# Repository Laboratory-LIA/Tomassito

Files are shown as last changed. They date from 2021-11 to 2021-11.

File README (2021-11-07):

README Tomassito V 0.9

The RobotCar Tomassito project is a development of "Applied Innovation Laboratory" of the informatics area
of the Santo Tomás Professional Institute, San Joaquín Campus.

Project distributed under Creative Commons Attribution License CC BY

Feel free to generate derivative developments, share and build robot, let's democratize technology.

Make us happy, follow our project

https://github.com/Laboratory-LIA/Tomassito/

/-/-/-/-/-/-/-/-/-/-/-/-/-/-/-/-/-/-/-/

README Tomassito V 0.9

El proyecto de RobotCar Tomassito es un desarrollo de "Laboratorio de Innovación Aplicada" del área de informática
del Instituto profesional Santo Tomás sede San Joaquín.

Proyecto distribuido bajo Licencia Creative Commons de Atribución CC BY

Siéntase libre de generar desarrollos derivados, compartir y construir robot, democraticemos la tecnología.

haznos felices, sigue nuestro proyecto

https://github.com/Laboratory-LIA/Tomassito/

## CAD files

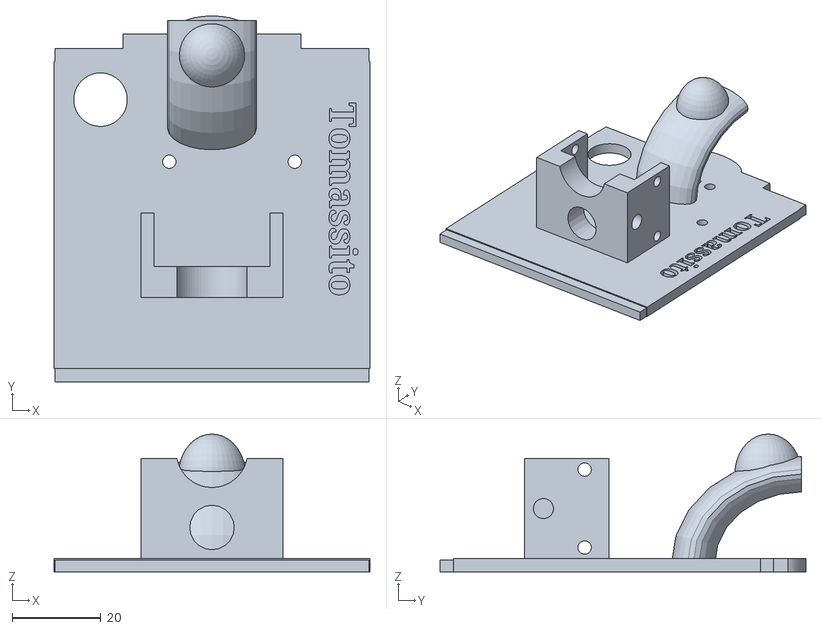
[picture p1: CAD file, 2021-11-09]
STL V0.9/Base.stl
71.0 x 82.3 x 31.0

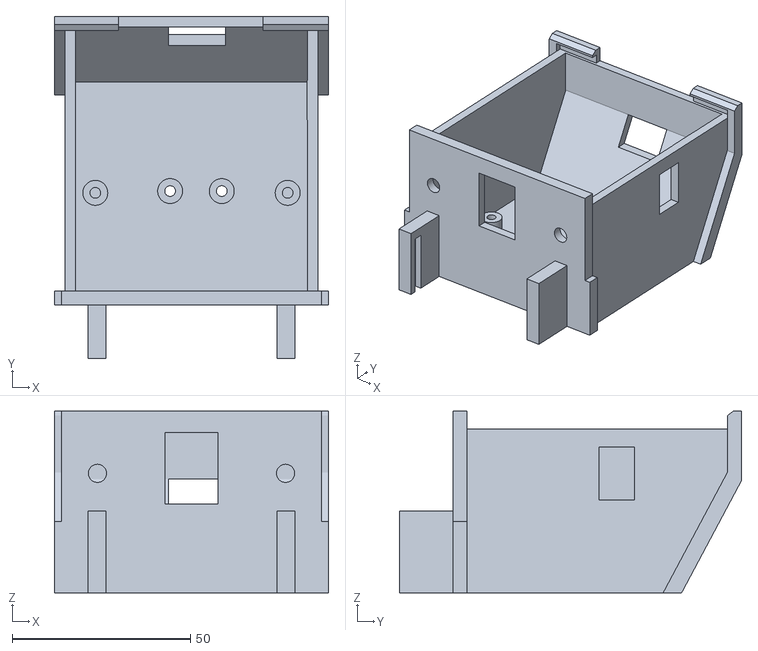
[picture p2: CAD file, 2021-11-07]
STL V0.9/Cuerpo.stl
77.0 x 96.0 x 51.0

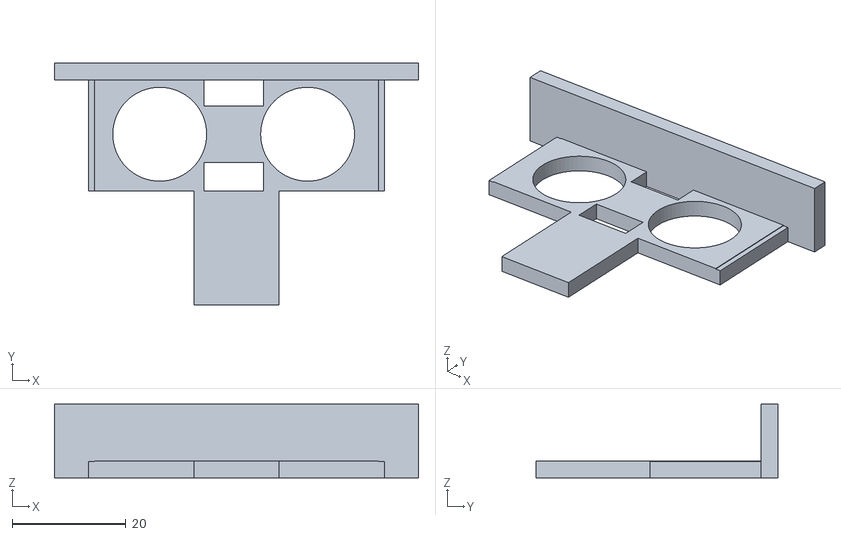
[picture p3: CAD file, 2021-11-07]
STL V0.9/Ojos.stl
64.0 x 42.5 x 13.0

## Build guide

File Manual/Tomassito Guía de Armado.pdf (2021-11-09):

| 2021

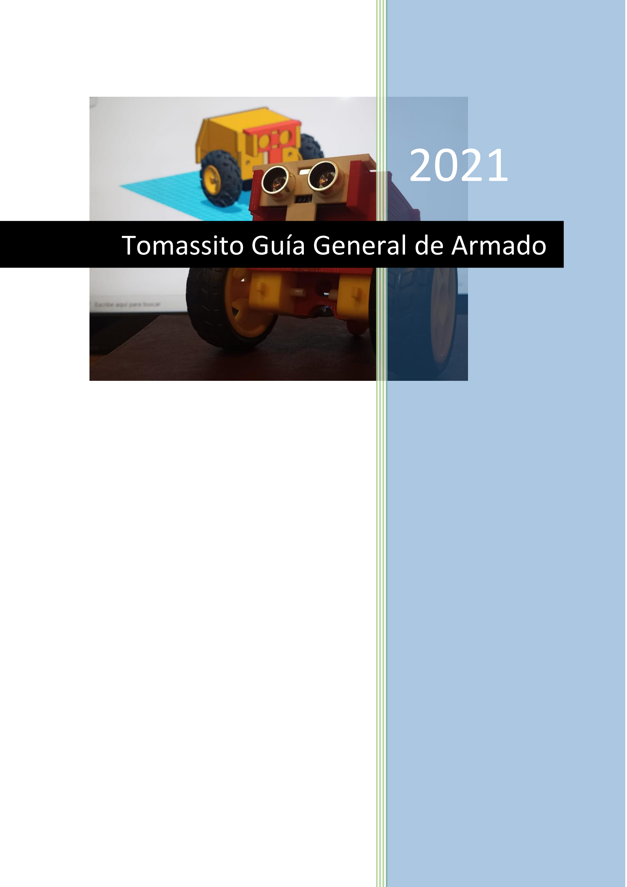
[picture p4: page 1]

# Tomassito Guía General de Armado

Laboratorio de Innovación Aplicada – LIA – Área de Informática | IPST
Tomassito – Guía General de Armado V0.5 | 1

## Contenido

Robot Tomassito Guía de Armado | 2
Lista de herramientas y materiales necesarios | 2
Impresión del RobotCar | 3
Comentarios Previos | 3
Impresión | 3
Pasos de armado | 3
1.- Limpieza de la impresión | 3
2.- Los ojos del robot | 4
3.- En el cuerpo del robot | 4
4.- En la base del robot | 5
Esquema de Cableado | 8
Pines y GPIO de Tomassito | 10
Finalizando el montaje | 10
Apertura y cierre de Tomassito | 11
Tabla 1: Lista de componentes y materiales | 2
Tabla 2: Lista de herramientas | 2
Tabla 3: Pines y nomenclatura | 10
Imagen 1: puntos de pulido base y cuerpo | 3
Imagen 2: Punto de pulido de los ojos | 4
Imagen 3: Montaje del sensor de ultrasonido | 4
Imagen 4: Montaje de porta pilas, leds y ojos | 5
Imagen 5: Estañado y soldado de los cables en los motores | 6
Imagen 6: Instalación del buzzer, shield y motores | 7
Imagen 7:cableado previo para pruebas, sin pasar por los orificios | 7
Imagen 8: Monitor serie, código de prueba general | 8
Imagen 9: Esquema simplificado de cableado | 9
Imagen 10: Posición final del cableado, post prueba de los componentes | 10
Imagen 11: Tomassito terminado | 11
Imagen 12: Puntos de apoyo para apertura y cierre | 11
Imagen 13: Forma de cierre de Tomassito | 12
Imagen 14: Forma de abrir el robot | 12

Robot Tomassito Guía de Armado

Lista de herramientas y materiales necesarios

Lista de materiales
Ítem | Cantidad | Descripción | Comentario
1 | 1 | Microcontrolador NodeMCU
2 | 1 | Shield NodeMCU | En algunos sitios web le llaman puente H
3 | 1 | Impresión Tomassito | Compuesto por la base, ojos y cuerpo
4 | 2 | Motorreductores | Debe incluir el neumático, en algunos sitios lo venden por separado
5 | 1 | Buzzer
6 | 4 | tornillos M3x5 | 2 para montar NodeMCU y 2 para el porta pilas
7 | 1 | Porta pilas AAx4
8 | 4 | Pernos tipo cocina 1/8 x 1 1/2 pulgada | Pueden usarse tonillos M3x40, pero el perno cocina de 1/8 evita usar tuercas
9 | 2 | Led de 5 mm | idealmente de colores distintos
10 | 1 | Sensor ultrasónico | HR-SR04
11 | 1 metro | Estaño | Soldadura preparada estaño plomo de 1 mm, es la mínima cantidad que venden, aunque se utiliza menos.
12 Los | necesarios | Cables Dupont HH
13 | 1 | Lija, cúter o lima | Papel de lija de grano 120 o un cúter para limpiar los bordes, también es posible utilizar una lima pequeña.

Tabla 1: Lista de componentes y materiales

Herramientas
Ítem | Cantidad | Descripción
1 | 1 | Alicate cortante
2 | 1 | Destornillado tipo cruz
3 | 1 | Cautín
Tabla 2: Lista de herramientas.

Impresión del RobotCar
Comentarios Previos
Los archivos para necesarios para la fabricación del RobotCar Tomassito pueden ser descargados desde nuestro Github, en este espacio almacenamos la versión más reciente del proyecto, también pueden encontrar código de ejemplo para el uso del básico del Robot

https://github.com/Laboratory-LIA/Tomassito

El diseño fue realizado en la plataforma de Tinkercad® y si desean realizar un trabajo derivado o modificar según sus requerimientos pueden clonar el modelo desde el siguiente enlace:

https://www.tinkercad.com/things/4OQldKZ7b8x

Impresión
El laminado de los archivos STL fue realizado en Ultimate Cura 4.11, con las siguientes características, se utilizó una impresora Ender 3 V2.
- Material PLA 1.75 mm
- Relleno al 20%
- Sin Soportes
- Laminado a capa de 0.2 mm

Posterior a la impresión los bordes son pulidos levemente para garantizar el encaje de las piezas para quitas los excesos de material, se puede realizar con un papel de lija de grano 120 o muy cuidadosamente con un cúter o una lima fina.

Pasos de armado.
1.- Limpieza de la impresión
Comentario Previo: La limpieza y pulido de los bordes y cantos en el robot simplifica posteriormente el armado y desarmado de Tomassito, el desgaste debe ser realizado cuidadosamente y dependiendo de la calidad de la impresora 3D y calidad de impresión en ciertas ocasiones no es necesario.

Limpiar los bordes de la impresión especialmente en los puntos en encaje entre el cuerpo, base y ojos. El orificio del buzzer debe ser limpiado muy levemente, se recomiendo ir probando su calce.

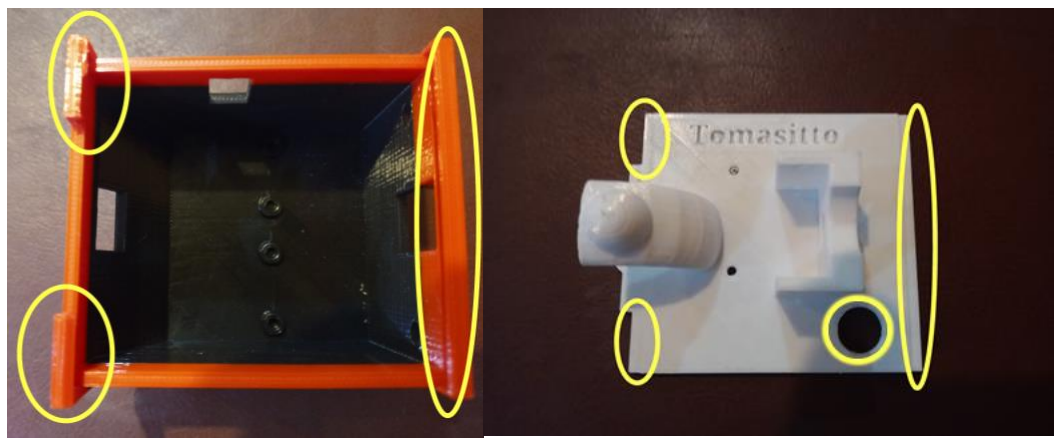
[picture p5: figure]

Imagen 1: puntos de pulido base y cuerpo.

En el caso de los ojos del robot, pulir internamente e ir revisando el calce con el sensor ultrasónico.

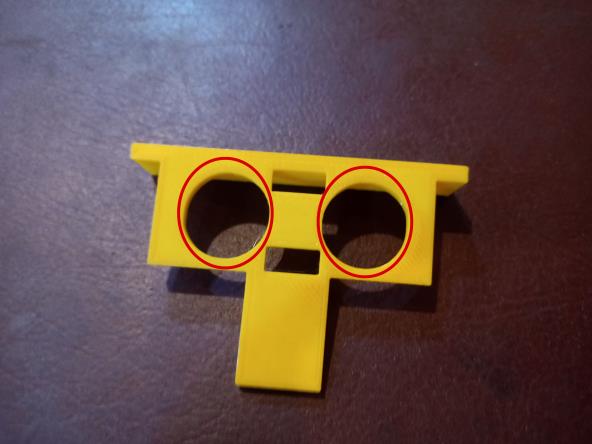
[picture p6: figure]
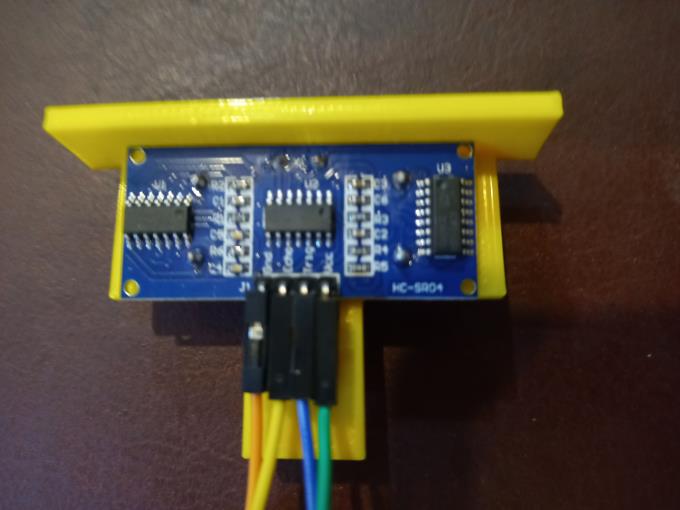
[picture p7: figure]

Tomassito – Guía General de Armado V0.5

4

Imagen 2: Punto de pulido de los ojos.

2.- Los ojos del robot
Montar el sensor ultrasónico y colocar 4 cables Dupont hembra-hembra.

Imagen 3: Montaje del sensor de ultrasonido.

3.- En el cuerpo del robot.
a.- Instalar el porta pilas con dos tornillos, a pesar de que cuenta con 4 orificios los porta pilas no están estandarizados y cada fabricante centra las fijaciones en función del diseño de su producto, los orificios del robot están pensados para ser usados con los modelos más comunes del mercado nacional, por esa razón se utilizan solo dos orificios. Los cables del porta pilas deben quedar hacia la parte trasera del cuerpo.

b.- Colocar los leds¹
y cortar los terminales a 1 cm para permitir colocar cables Dupont hembra-hembra.

c.- Montar los ojos en el cuerpo de Tomassito y pasar a través de la abertura los cables Dupont hacia el interior.

1
Se debería agregar una resistencia para limitar la corriente en función del umbral de voltaje del led, pero al usarse el NodeMCU es muy cercando, si considera un uso constante de los leds, considere calcular una resistencia limitadora y agregarla a Tomassito.

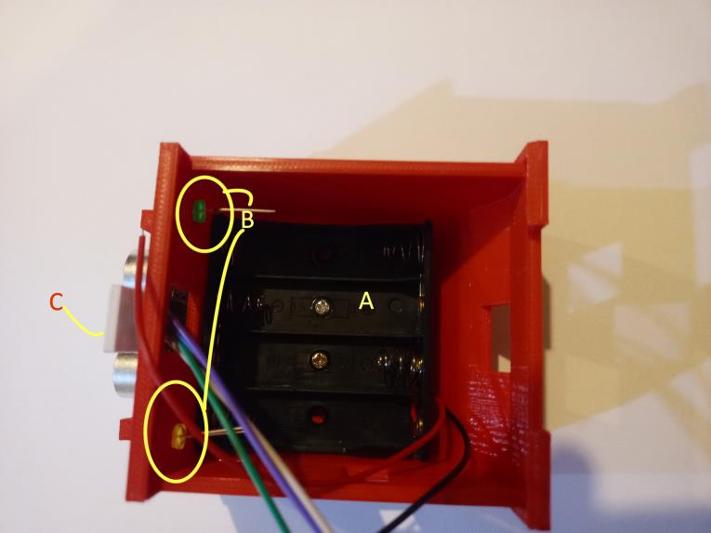
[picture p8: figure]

Tomassito – Guía General de Armado V0.5

5

Imagen 4: Montaje de porta pilas, leds y ojos.

4.- En la base del robot.

Comentario Previo: los contactos de los motorreductores son sumamente frágiles, el proceso se debe hacer con paciencia.

a.- Estañar (con el cautín y la soldadura) 4 cables de AWG-28, mismo calibre que los cables Dupont, se puede cortar 4 cables Dupont para el proceso (no es necesario un calibre mayor, debido a que el porta pilas usa el mismo tamaño)²

b.- Una vez frío el cable introducir por el orificio del contacto del motor.

c.- Agregar un punto de soldadura con el cautín para unir el cable estañado y el contacto del motor, finalmente con precaución cortar el excedente (si es que existe) del cable estañado.

2
Si por consumo se quema algún conductor, la primera línea en fallar será la del porta pilas, por ello no es necesario un calibre mayor para los motores, la corriente queda limitada por ese conductor.

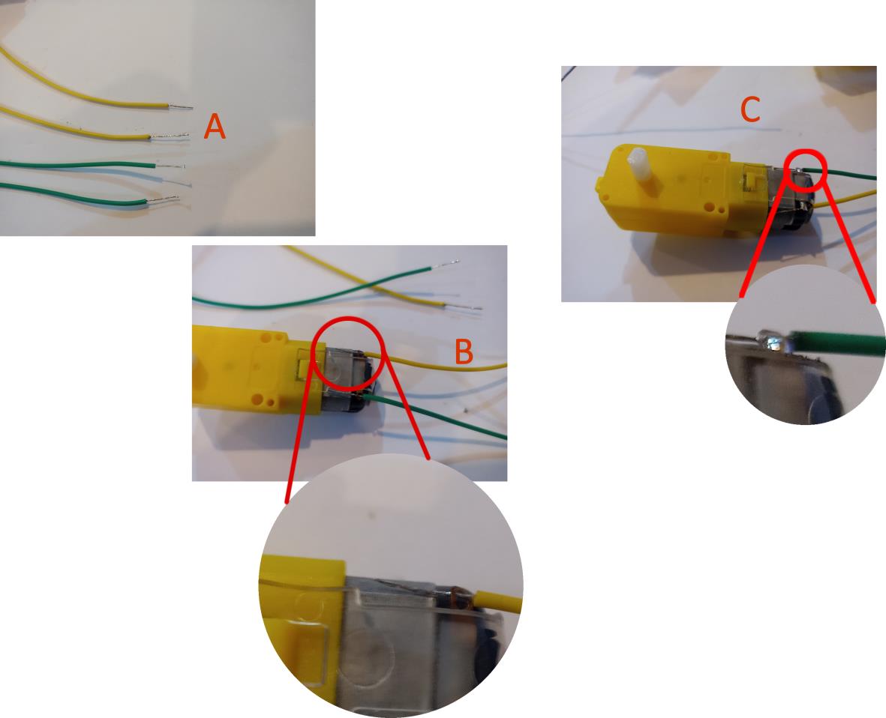
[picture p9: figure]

Tomassito – Guía General de Armado V0.5

6

Imagen 5: Estañado y soldado de los cables en los motores.

d.- Instalar el buzzer.

e.- Instalar el Shield, usando dos tornillos M3 por 5 milímetros, nota importante SOLO SHIELD, sin el NodeMCU.

f.- Instalar los motores con 2 pernos de cocina de 1/8 por 1 ½ pulgada³

g.- Montar el NodeMCU.

3
Se prefiere este tipo de elemento de sujeción pues evita el uso de tuercas y genera hilo en la impresión del robot, si utiliza tornillos M3 para montar los motorreductores DEBE utilizar tuercas.

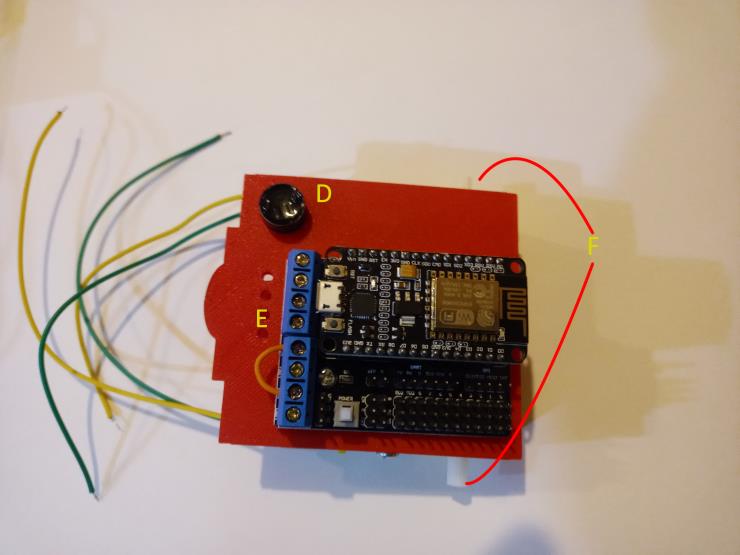
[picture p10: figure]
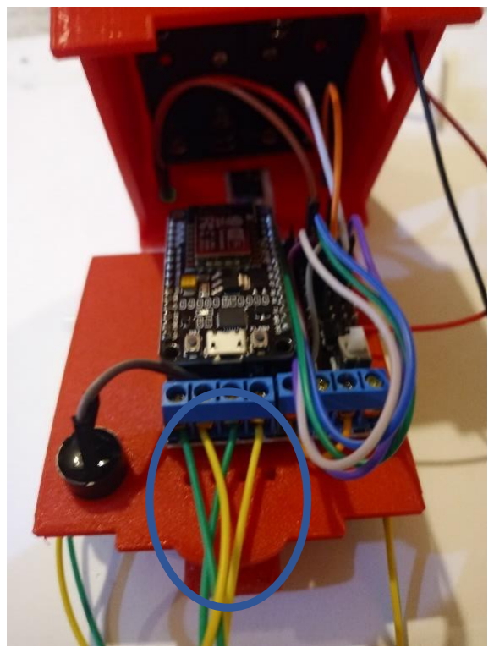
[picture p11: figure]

Tomassito – Guía General de Armado V0.5

7

Imagen 6: Instalación del buzzer, shield y motores.

En este punto podemos realizar el cableado según el esquema que sale más adelante, a modo de sugerencia no dar la posición definitiva de los motores y pasar los cables por fuera de los orificios y probar con un código⁴ el funcionamiento de todos los componentes se puede visualizar por el monitor serie cada uno de los elementos, si los motores están en sentido contrario, la solución es simple, cambiar el + por el – en el cableado (para el motor A o B, incluso para ambos)

Imagen 7:cableado previo para pruebas, sin pasar por los orificios.

4 Desde le GitHub pueden descargar el código de prueba, https://github.com/Laboratory-LIA/Tomassito/tree/main/Examples/Test_General_Componentes (https://github.com/Laboratory-LIA/Tomassito/tree/main/Examples/Test_General_Componentes)

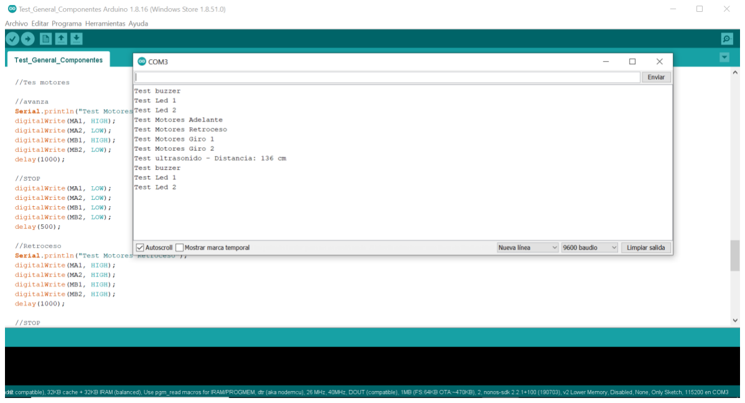
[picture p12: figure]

Tomassito – Guía General de Armado V0.5

8

El código de prueba nos permite visualizar, por el monitor serie del ide de Arduino, que parte del código se está ejecutando, con lo cual podemos verificar el sentido de movimiento de los motores (adelante y atrás), el funcionamiento del sensor ultrasónico y resto de elementos del robot, como se indicó anteriormente si el sentido de los motores es incorrecto la solución es simple, invertir la posición del + y – en el cableado. Se sugiere en esta prueba previa realizarla sin las ruedas.

Importante: No olvidar encender el shield, en algunos modelos se requiere que este encendido para que los motores funcionen.

Imagen 8: Monitor serie, código de prueba general

Esquema de Cableado.

5
El siguiente corresponde al esquema de cableado simplificado de Tomassito, un punto importante a señalar que no es necesario realizar un puente entre los GND del Shield puesto que es interno (a diferencia del puente realizado en el VIN y la alimentación de los motores)

5 Puede descargar un archivo PDF desde el GitHub para mayor resolución de la imagen. https://github.com/Laboratory-LIA/Tomassito/blob/main/Manual/Wiring%20tomassito.pdf

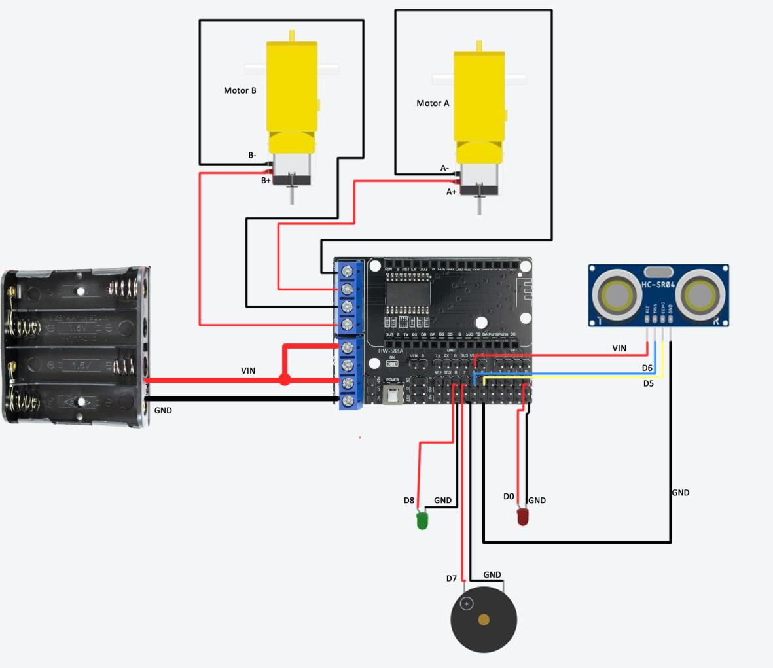
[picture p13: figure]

Imagen 9: Esquema simplificado de cableado.

Pines y GPIO de Tomassito.
Si desea realizar alguna modificación, proyecto derivado o incluso la siguiente tabla es útil para la saber los pines al momento de programar a Tomassito.
Nomenclatura en el shield | Uso | GPIO | Comentario
D0 | LED 01 | 16 | LED 01
D1 | MOTOR SHIELD | 5 | Motor A1
D2 | MOTOR SHIELD | 4 | Motor A2
D3 | MOTOR SHIELD | 0 | Motor B1
D4 | MOTOR SHIELD | 2 | Motor B2
D5 | ECHO | 14 | Sensor HC-SR04
D6 | TRIG | 12 | Sensor HC-SR04
D7 | BUZZER | 13 | Zumbador
D8 | LED 02 | 15 | LED 02
Tabla 3: Pines y nomenclatura

Finalizando el montaje
Una vez verificado el correcto funcionamiento de los componentes y sentido de los motores, se la disposición final de los cables de Tomassito.

Montamos las pilas

Cerramos a Tomassito

Finalmente, colocamos las ruedas.

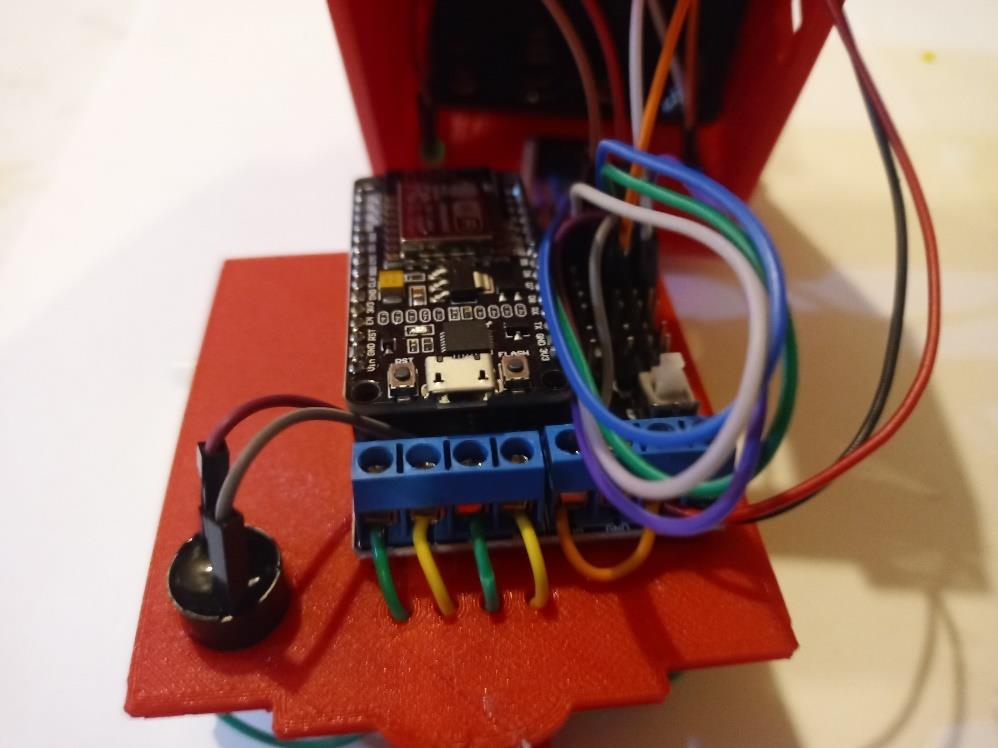
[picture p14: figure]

Imagen 10: Posición final del cableado, post prueba de los componentes

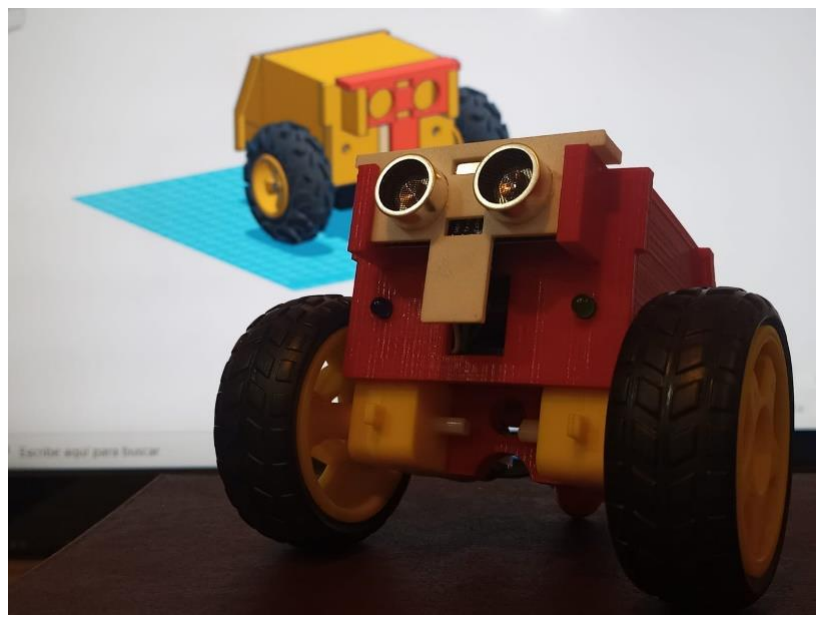
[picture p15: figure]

Imagen 11: Tomassito terminado.

Apertura y cierre de Tomassito
Tanto para la apertura como para el cierre de Tomassito la fuerza debe ser aplicada sobre la parte posterior de la base con el pulgar de una mano, con la otra mano sostener entre el índice y el pulgar el cuerpo del robot. NUNCA APLICAR FUERZA SOBRE EL SOPORTE DE LA BASE.

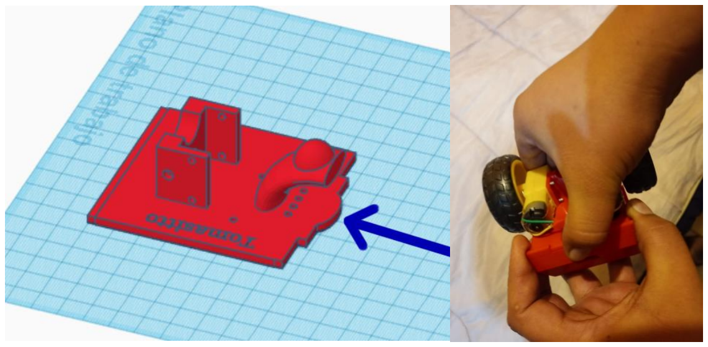
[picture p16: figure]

Imagen 12: Puntos de apoyo para apertura y cierre.

Para cerrar el robot se debe introducir en ángulo y posteriormente presionar como indica la flecha en la siguiente imagen.

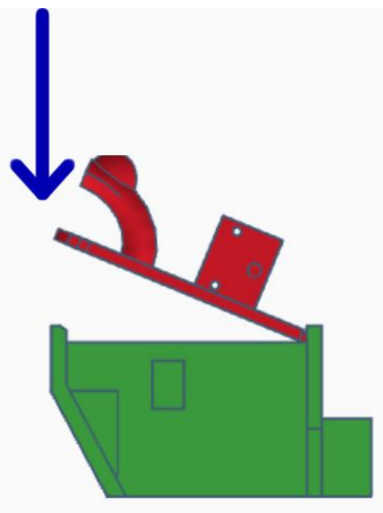
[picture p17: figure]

Imagen 13: Forma de cierre de Tomassito.

Para la apertura del robot presionar hacia adentro con el pulgar y jalar hacia afuera con la otra mano

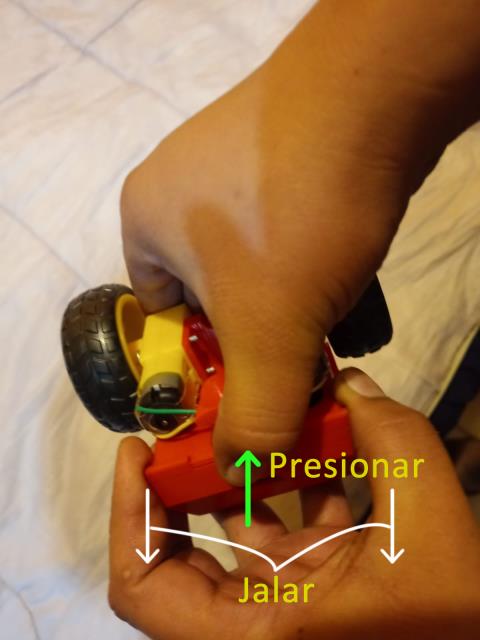
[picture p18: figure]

Imagen 14: Forma de abrir el robot.

## <<Gracias por construir un Tomassito, democraticemos la tecnología>>

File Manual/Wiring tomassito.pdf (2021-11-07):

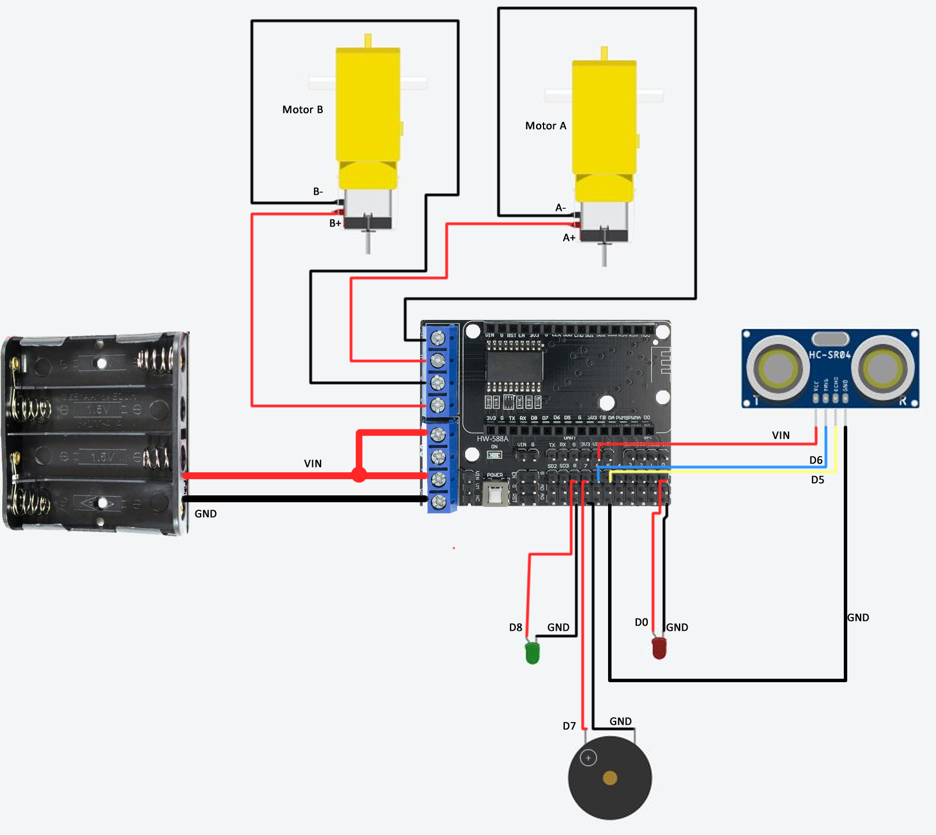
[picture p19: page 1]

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
Motor B
Motor A

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
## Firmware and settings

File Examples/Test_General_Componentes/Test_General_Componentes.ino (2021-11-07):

//Test General de componentes Tomassito V0.9

  //Sensor ultrasonico

  #define echoPin 14
  #define trigPin 12

  long duration;
  int distance; 

  // Motor dirección

  int MB2 = 2;
  int MB1 = 4;
  int MA2 = 0;
  int MA1 = 5;

  //Led

  int led2 = 15;
  int led1 = 16;

  //Buzzer
  
  int buzzer = 13;
  int cuarto = 1000 / 4;
  int octavo = 1000 / 8;
  double pausa = 1.30;
  int NOTA_A1 = 55; 
  int NOTA_F6 = 1479;
  int NOTA_E5 = 659; 
  int NOTA_C3 = 130; 

void setup() {
  
  pinMode(trigPin, OUTPUT);
  pinMode(echoPin, INPUT);
  
  Serial.begin(9600);
  
  Serial.println("Test General ...");
  Serial.println("Tomasitto V0.9");
  
  pinMode(MB2, OUTPUT);     
  pinMode(MB1, OUTPUT);
  pinMode(MA2, OUTPUT);
  pinMode(MA1, OUTPUT);
  
  pinMode(led1 , OUTPUT); 
  pinMode(led2 , OUTPUT);
  
  pinMode(buzzer, OUTPUT);
}

void loop() {

  // Test ultrasonido
  
  Serial.print("Test ultrasonido - ");
  delay(1000);
  digitalWrite(trigPin, LOW);
  delayMicroseconds(2);
  digitalWrite(trigPin, HIGH);
  delayMicroseconds(10);
  digitalWrite(trigPin, LOW);  
  duration = pulseIn(echoPin, HIGH);
  distance = duration * 0.034 / 2;
  Serial.print("Distancia: ");
  Serial.print(distance);
  Serial.println(" cm");
  delay(5000);

  //test buzzer
  
  Serial.println("Test buzzer");
  tone(buzzer, NOTA_A1, octavo);
  delay(octavo*pausa);
  tone(buzzer, NOTA_A1, octavo);
  delay(octavo*pausa);
  tone(buzzer, NOTA_F6, octavo);
  delay(octavo*pausa);
  tone(buzzer, NOTA_E5, octavo);
  delay(octavo*pausa);
  tone(buzzer, NOTA_A1, octavo);
  delay(octavo*pausa);
  noTone(buzzer);
  delay(125);
  tone(buzzer, NOTA_C3, cuarto);
  delay(cuarto*pausa);
  tone(buzzer, NOTA_A1, octavo);
  delay(octavo*pausa);
  tone(buzzer, NOTA_A1, octavo);
  delay(octavo*pausa);
  tone(buzzer, NOTA_F6, octavo);
  delay(octavo*pausa);
  tone(buzzer, NOTA_E5, octavo);
  delay(octavo*pausa);
  tone(buzzer, NOTA_A1, octavo);
  delay(octavo*pausa);
  noTone(buzzer);
  delay(125);
  tone(buzzer, NOTA_F6, cuarto);
  delay(cuarto*pausa);
  delay(1000);

  // Test leds
  
  Serial.println("Test Led 1");
  digitalWrite(led1, HIGH);
  delay(500);
  digitalWrite(led1, LOW);
  delay(500);
  digitalWrite(led1, HIGH);
  delay(500);
  digitalWrite(led1, LOW);
  delay(500);
  digitalWrite(led1, HIGH);
  delay(500);
  digitalWrite(led1, LOW);
  delay(500);
  digitalWrite(led1, HIGH);
  delay(500);
  digitalWrite(led1, LOW);
  delay(500);
  Serial.println("Test Led 2");
  digitalWrite(led2, HIGH);
  delay(500);
  digitalWrite(led2, LOW);
  delay(500);
  digitalWrite(led2, HIGH);
  delay(500);
  digitalWrite(led2, LOW);
  delay(500);
  digitalWrite(led2, HIGH);
  delay(500);
  digitalWrite(led2, LOW);
  delay(500);
  digitalWrite(led2, HIGH);
  delay(500);
  digitalWrite(led2, LOW);
  delay(500);
  
  //Tes motores
    
  //avanza
  Serial.println("Test Motores Adelante");
  digitalWrite(MA1, HIGH);
  digitalWrite(MA2, LOW);
  digitalWrite(MB1, HIGH);
  digitalWrite(MB2, LOW);
  delay(1000); 
   
  //STOP
  digitalWrite(MA1, LOW);
  digitalWrite(MA2, LOW);
  digitalWrite(MB1, LOW);
  digitalWrite(MB2, LOW);
  delay(500);

  //Retroceso
  Serial.println("Test Motores Retroceso");
  digitalWrite(MA1, HIGH);                 
  digitalWrite(MA2, HIGH);
  digitalWrite(MB1, HIGH);                              
  digitalWrite(MB2, HIGH); 
  delay(1000);

  //STOP
  digitalWrite(MA1, LOW);
  digitalWrite(MA2, LOW);
  digitalWrite(MB1, LOW);
  digitalWrite(MB2, LOW);
  delay(500);

  //Giro 1
  Serial.println("Test Motores Giro 1");
  digitalWrite(MA1, HIGH);           
  digitalWrite(MA2, LOW);
  digitalWrite(MB1, HIGH);                           
  digitalWrite(MB2, HIGH);
  delay(1000); 

  //STOP
  digitalWrite(MA1, LOW);
  digitalWrite(MA2, LOW);
  digitalWrite(MB1, LOW);
  digitalWrite(MB2, LOW);
  delay(500);
     
  //Giro 2
  Serial.println("Test Motores Giro 2");
  digitalWrite(MA1, HIGH);               
  digitalWrite(MA2, HIGH);
  digitalWrite(MB1, HIGH);                            
  digitalWrite(MB2, LOW); 
  delay(1000); 
   
  //STOP
  digitalWrite(MA1, LOW);
  digitalWrite(MA2, LOW);
  digitalWrite(MB1, LOW);
  digitalWrite(MB2, LOW);
  delay(500);
   
  }
  

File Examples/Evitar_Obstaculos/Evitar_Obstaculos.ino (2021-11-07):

/*
La distancia de 50 cm definido en el IF puede ser adecuado según requerimientos
Los delay de los movimientos de los motores pueden ajustarse para mejorar el funcionamiento

*/ 


//Evitar obstaculos

//Sensor ultrasonico

#define echoPin 14
#define trigPin 12

long duration;
int distance; 

// Motor dirección

int MB2 = 2;
int MB1 = 4;
int MA2 = 0;
int MA1 = 5;

//Led

int led1 = 15;
int led2 = 16;

//Buzzer

int buzzer = 13;



void setup() {

  pinMode(trigPin, OUTPUT);
  pinMode(echoPin, INPUT);
  
  Serial.begin(9600);
  
  Serial.println("Sensor HC-SR04");
  Serial.println("Tomasitto");
  
  pinMode(MB2, OUTPUT);     
  pinMode(MB1, OUTPUT);
  pinMode(MA2, OUTPUT);
  pinMode(MA1, OUTPUT);
  
  pinMode(led1 , OUTPUT); 
  pinMode(led2 , OUTPUT);
  
  pinMode(buzzer, OUTPUT);
  
}

void loop() {
  
  digitalWrite(trigPin, LOW);
  delayMicroseconds(2);
  
  digitalWrite(trigPin, HIGH);
  delayMicroseconds(10);
  digitalWrite(trigPin, LOW);  
  
  duration = pulseIn(echoPin, HIGH);
  
  distance = duration * 0.034 / 2;
  
  Serial.print("Distancia: ");
  Serial.print(distance);
  Serial.println(" cm");
  
  if (distance > 50)
  {
    digitalWrite(led1, HIGH);
    digitalWrite(led2, LOW);
    
    //avanza
    digitalWrite(MA1, HIGH);
    digitalWrite(MA2, LOW);
    digitalWrite(MB1, HIGH);
    digitalWrite(MB2, LOW);
    delay(500);  

  }

  if (distance < 50)
  {
    digitalWrite(led1, LOW);
    digitalWrite(led2, HIGH);
    tone(buzzer, 500);
    delay(250);        
    noTone(buzzer);   
    delay(250);
    tone(buzzer, 800);
    delay(250);        
    noTone(buzzer);   
    delay(250);     
    
    //STOP
    digitalWrite(MA1, LOW);
    digitalWrite(MA2, LOW);
    digitalWrite(MB1, LOW);
    digitalWrite(MB2, LOW);
    delay(500);

    //retroceso
    digitalWrite(MA1, HIGH);                 
    digitalWrite(MA2, HIGH);
    digitalWrite(MB1, HIGH);                              
    digitalWrite(MB2, HIGH); 
    delay(500);

    //STOP 
    digitalWrite(MA1, LOW);
    digitalWrite(MA2, LOW);
    digitalWrite(MB1, LOW);
    digitalWrite(MB2, LOW);
    delay(500);

    //giro
    digitalWrite(MA1, HIGH);                  
    digitalWrite(MA2, LOW);  
    digitalWrite(MB1, HIGH);                               
    digitalWrite(MB2, HIGH);   
    delay(500);
    
  }

}

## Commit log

2021-11-07 STL V0.9
    First production version of Tomassito
    [Base.stl, Cuerpo.stl, Ojos.stl]
2021-11-07 Create Wiring tomassito.pdf
    Wiring picture
2021-11-07 Actualización STL
    Correcciones menores
    [Base.stl, Cuerpo.stl]
2021-11-08 Create Tomassito Guía de Armado.pdf
2021-11-09 Update Tomassito Guía de Armado.pdf
    Correcciones menores al documento general
2021-11-09 Update Base.stl
    Corrección menor del STL
    [Base.stl]
